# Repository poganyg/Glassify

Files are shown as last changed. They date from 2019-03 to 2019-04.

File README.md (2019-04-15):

<p align="center">
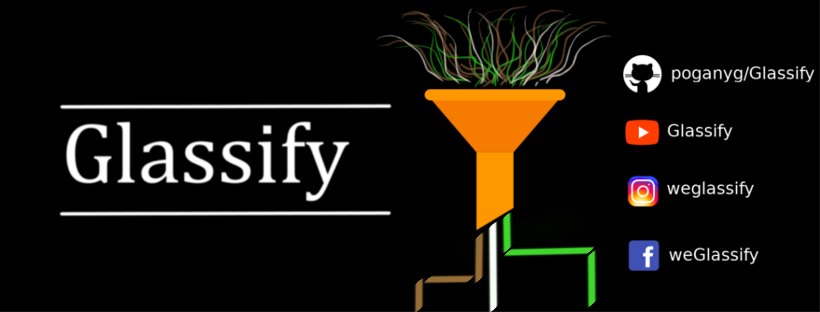
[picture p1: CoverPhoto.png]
Glassify cover photo
   
</p>

# Introduction

We are bringing you a colour-based glass recycling sorter which can separate, in real-time, green, amber and clear bottles!
This is a university project for the subject real-time embedded programming. Watch our short introduction to why and how we are building this project:

<p align="center">
  <a href="https://www.youtube.com/watch?v=iapjhaJnOS8" target="_blank">
  A video summary of Glassify 
  </a>
</p>

## Motive

Glass is 100% recyclable and by doing so we can substantially reduce raw materials needed, the waste produced as well as water and air pollution.<sup>[1](https://www.glassrecycle.co.uk/Why-Recycle/Facts--Figures/)</sup> However, contamination is a major factor in the effectiveness of recycling.<sup>[2](https://wasterecycling.org/news/426888/NWRA-Celebrates-America-Recycles-Day.htm)</sup> This can be due to non-glass materials disposed alongside with the bottles, such as bottle caps, but also by mixing differently coloured glasses. Colours are achieved by adding impurities, such as sulfur, copper or iron to the glasses. Their purpose is to protect the contents from environmental effects. Even one colour misplaced in the wrong bin can deteriorate the quality of the recycled glass. <sup>[3](https://recyclenation.com/2014/09/recycling-glass-does-color-matter/)</sup> This project aims to achieve a more effective glass recycling to preserve our natural resources and protect our environment. 

## Our Solution

We are presenting here a device which can be installed to recycling points to assisst with the user-side recycling process. Once installed, a single input can be used for the glass recycling bin and the internal sorting would ensure that colour contamination doesn't occur. The device uses a Raspberry Pi microcontroller and is built using 3D printing which means that the overall production cost can be kept under £100. 

<p align="center">
  <a href="https://www.youtube.com/watch?v=UAzmWVJm4zI" target="_blank">
  A video summary of Glassify 
  </a>
</p>

# Have we got your fascination?

To see updates follow us on Facebook, YouTube and Instagram.

If you would like to recreate this project, head over to our [Wiki](https://github.com/poganyg/Glassify/wiki) page where you will find a detailed building guide including a list of all the components you will need for building it. In terms of software requirements, you will need to install:

* [openCV](https://opencv.org/releases.html)
* [Raspicam](http://www.uco.es/investiga/grupos/ava/node/40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)
* [WiringPi](http://wiringpi.com/download-and-install/)
* [CMake](https://cmake.org/install/)
* [Git](https://git-scm.com/downloads) (Optional, makes cloning this repository easier.)

Do make sure to only have these installed once on your Raspberry Pi.

To build our software run the following code in your terminal:
```
git clone https://github.com/poganyg/Glassify.git
cd Glassify
mkdir build
cd build
cmake ..
make
```

The project is under the GNU General Public License v3.0.

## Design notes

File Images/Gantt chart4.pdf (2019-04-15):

ea
te Glassify | SIMPLE GANTT CHART by Vertex42.com (https://www.vertex42.com/ExcelTemplates/simple-gantt-chart.html)

Enter Company Name in cell B2. Ross Crawford

https://www.vertex42.com/ExcelTemplates/simple-gantt-chart.html

Enter the name of the Project Lead in cell B3. Enter the Project Start date in cell E3. Pooject Start: label is in cell C3. Reuben Docea | Project Start:

e
Di

### Gergely Pogany

Display Week:

1

lls | 11 12 13 14 15 16 17 | 18 19 20 21 22 23 24 | 25 26 27 28 1 2 3 | 4 5 6 7 8 9 10 | 11 12 13 14 15 16 17 | 18 19 20 21 22 23 24 | 25 26 27 28 29 30 31 | 1 2 3 4 5 6 7 | 8 9 10 11 12 13 14
is
ro
TASK | ASSIGNED
TO
START | END | M | T | W | T | F | S | S | M | T | W | T | F | S | S | M | T | W | T | F | S | S | M | T | W | T | F | S | S | M | T | W | T | F | S | S | M | T | W | T | F | S | S | M | T | W | T | F | S | S | M | T | W | T | F | S | S | M | T | W | T | F | S | S

ll
B8 Design and Setup

ll
B9 | Learning C++ | All | 10/02/19 | 28/02/19

o
w
Hardware Concept | All | 15/02/19 | 18/02/19
Installing Necessary Libraries | Reuben | 20/02/19 | 22/02/19
In-depth Hardware Design | Reuben + Ross | 22/02/19 | 02/03/19

e
ce

Software Development

LCD Scripts | Gergely | 01/03/19 | 10/03/19
Classification Scripts | Reuben | 01/03/19 | 19/03/19
Switch Polling | Ross | 04/03/19 | 11/03/19
Motor Scripts | Gergely | 06/03/19 | 12/03/19
Menu Coding | Gergely | 11/03/19 | 17/03/19
Compiling and Threading | Ross | 11/03/19 | 27/03/19

Sample phase title block Hardware Development

Ordering Suitable Components | Gergely | 02/03/19 | 03/03/19
Modelling Parts | Reuben + Ross | 02/03/19 | 13/03/19
PCB Design | Gergely | 02/03/19 | 13/03/19
Part Priniting | Reuben | 03/03/19 | 15/03/19
Assembly | All | 15/03/19 | 19/03/19

Sample phase title block Optimisation

Testing Software | Reuben | 28/03/19 | 03/04/19
Testing Hardware | Ross | 28/03/19 | 03/04/19
Improvements from Tests | All | 03/04/19 | 14/04/19

15/02/2019

Feb 11, 2019 | Feb 18, 2019 | Feb 25, 2019 | Mar 4, 2019 | Mar 11, 2019 | Mar 18, 2019 | Mar 25, 2019 | Apr 1, 2019 | Apr 8, 2019

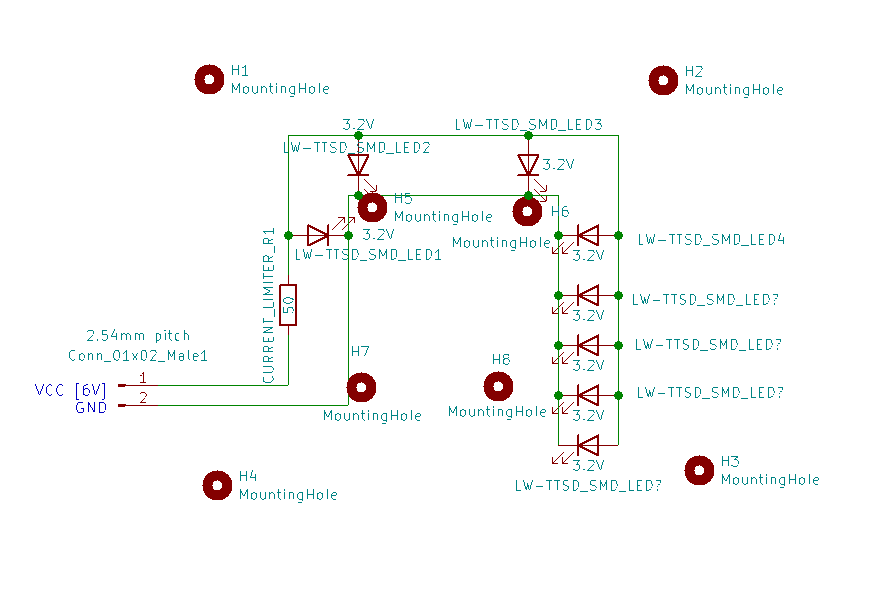
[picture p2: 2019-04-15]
Images/LED_board_schematic_cropped.png

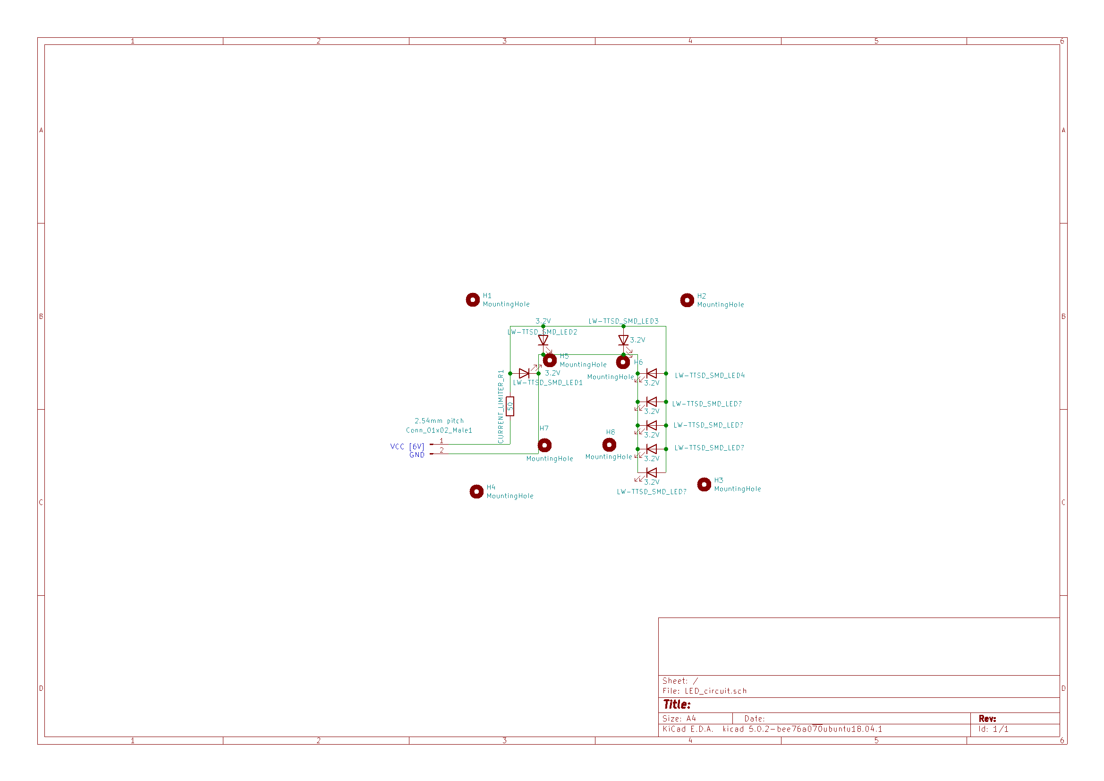
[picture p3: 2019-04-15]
Images/LED_board_schematic.png

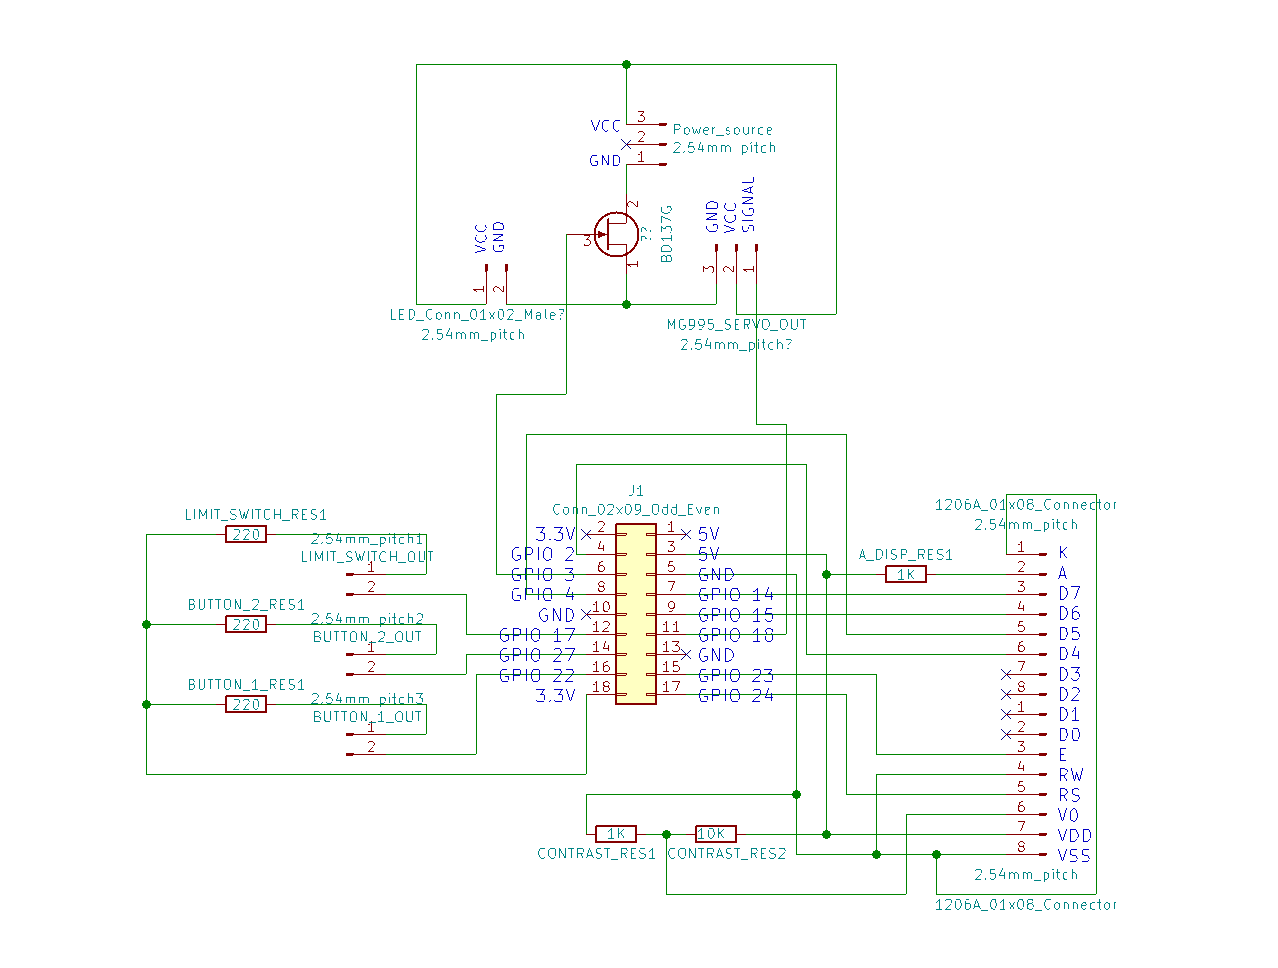
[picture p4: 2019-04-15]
Images/main_board_schematic_cropped.png

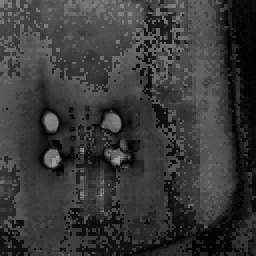
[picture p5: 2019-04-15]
Images/bottle03.jpg

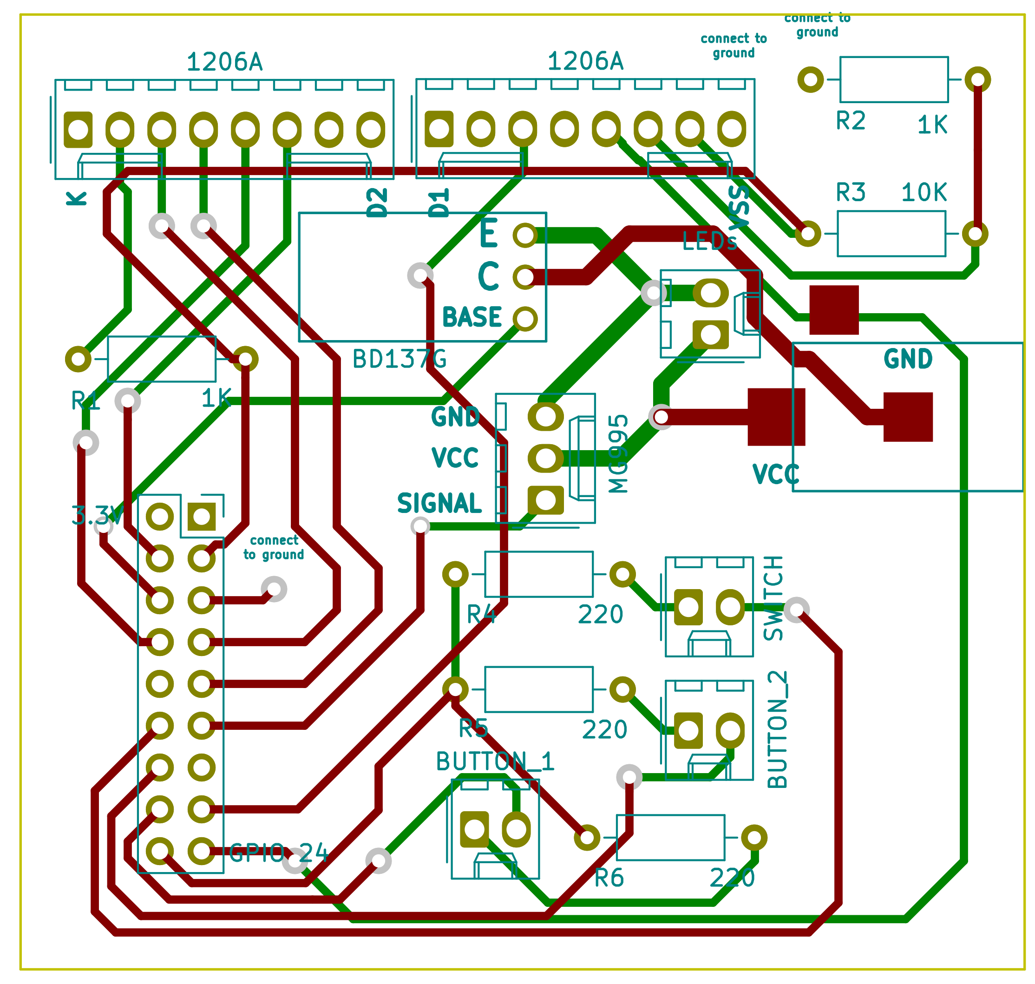
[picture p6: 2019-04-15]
Images/glassify-brd.png

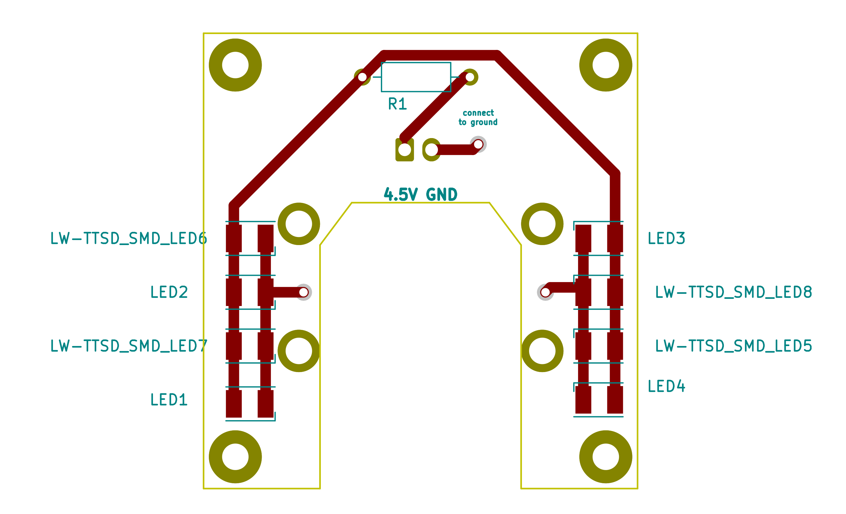
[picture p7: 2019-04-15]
Images/LED_circuit-brd.png

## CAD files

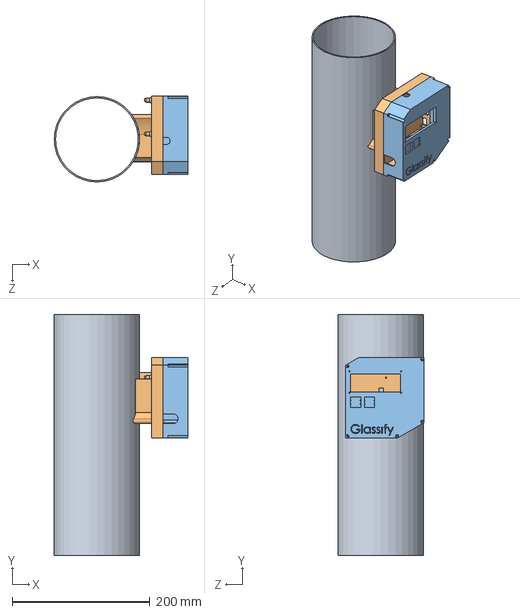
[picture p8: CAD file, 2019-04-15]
hardware/3DModels/Electronics/ElectronicsAssembly.SLDASM
194.0 x 350.0 x 124.8 mm
ElectronicsHousing
ElectronicsHousingCover

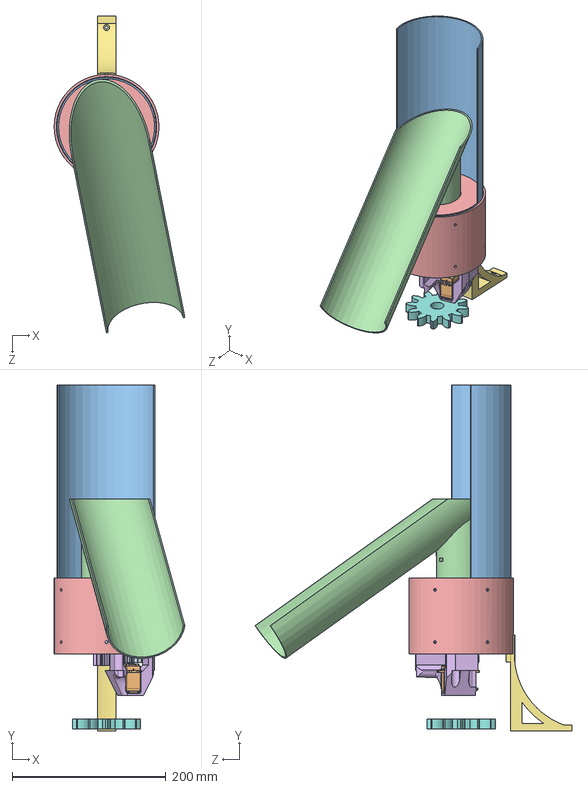
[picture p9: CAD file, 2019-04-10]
hardware/3DModels/Assembly.SLDASM
170.2 x 450.0 x 412.4 mm
WheelBarNarrower x 7
WheelEnlarged x 7
TopRing
ShaftClamp
ServoGear
ROBOT SERVO Hitec HSR-2645CR
BaseDrillGuide
NewServoCarriage
SorterStand

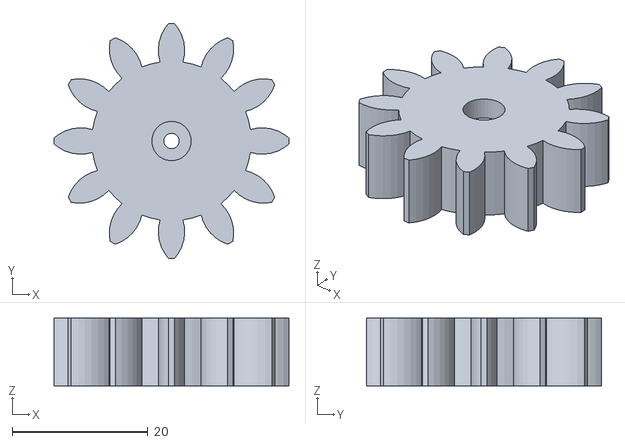
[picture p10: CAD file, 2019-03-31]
hardware/3DModels/STL Files/ServoGear.STL
34.7 x 34.7 x 10.0

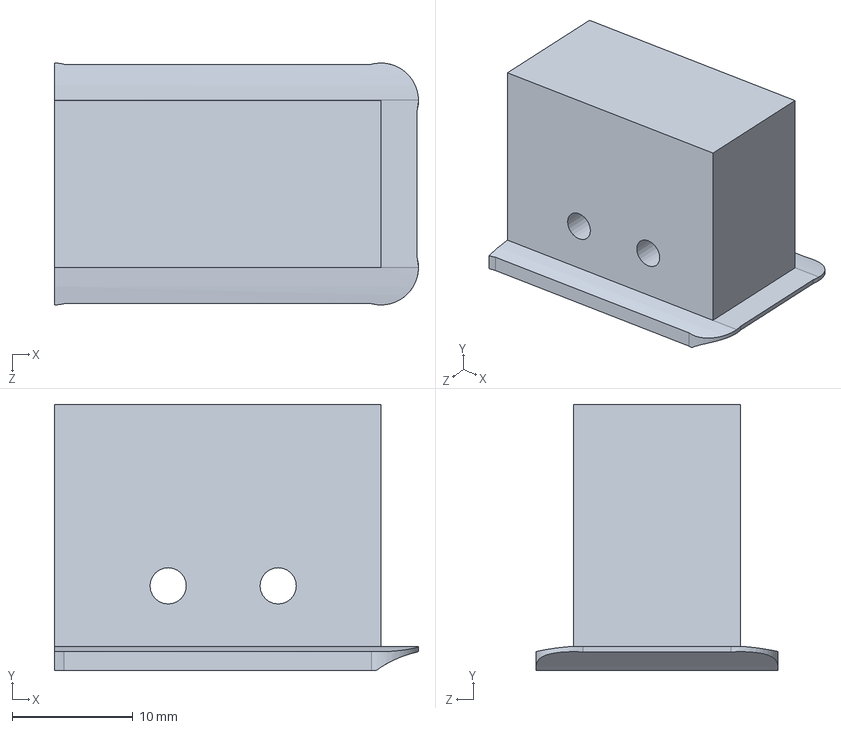
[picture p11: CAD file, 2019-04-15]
hardware/3DModels/switchHolder.SLDPRT
30.1 x 22.0 x 20.0 mm

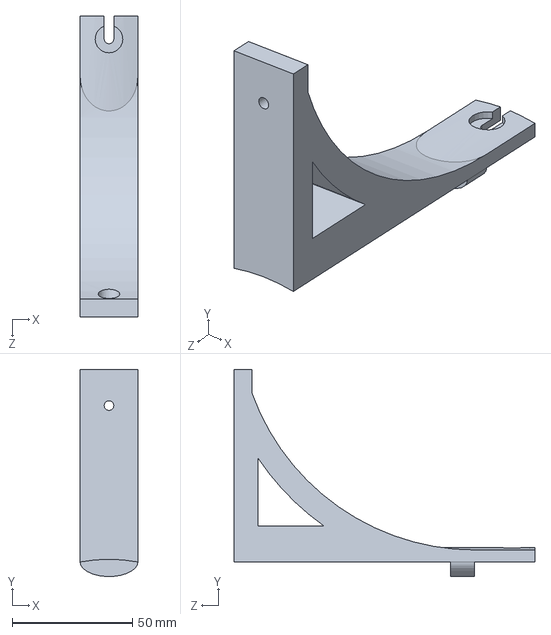
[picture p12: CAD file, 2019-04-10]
hardware/3DModels/SorterStand.sldprt
24.0 x 86.0 x 125.0 mm

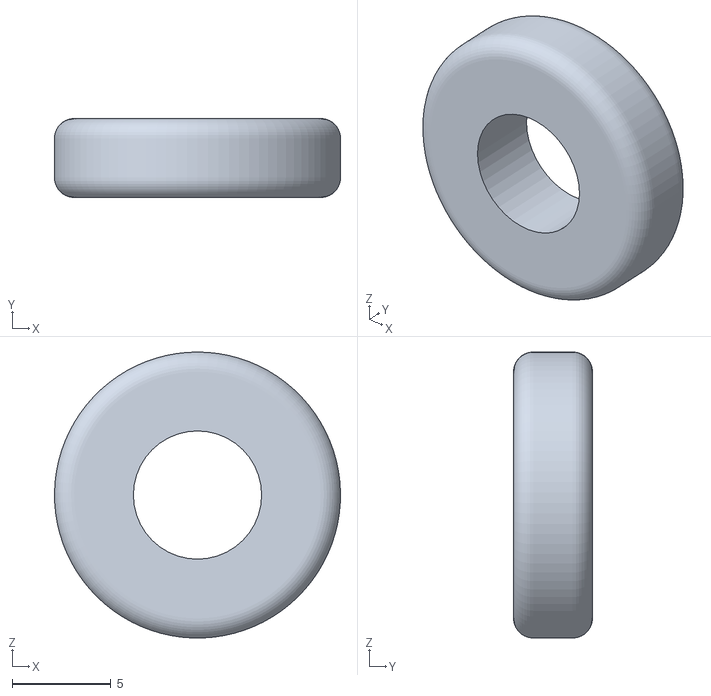
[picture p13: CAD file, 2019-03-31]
hardware/3DModels/STL Files/Wheel.STL
14.5 x 4.00 x 14.5

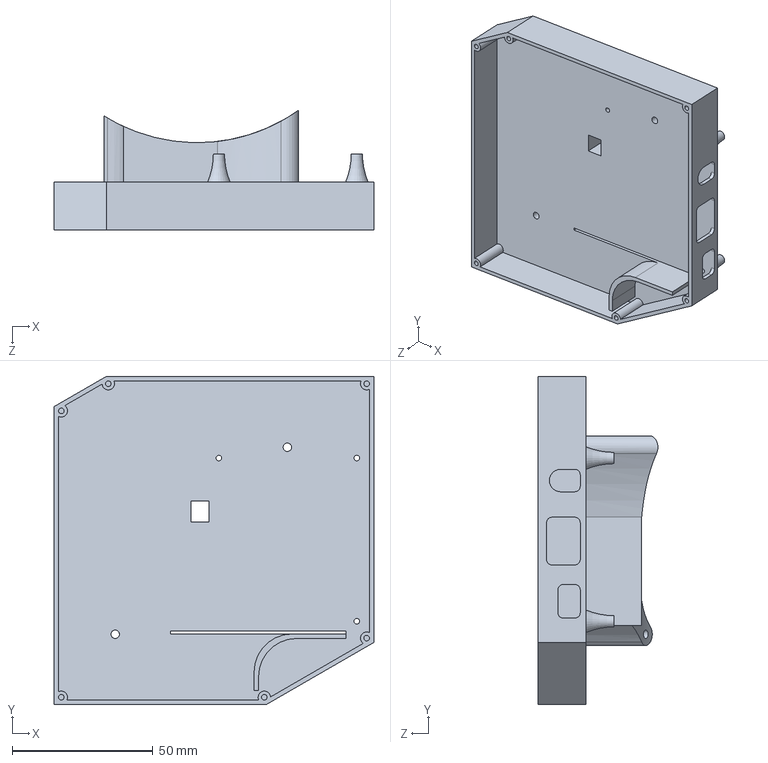
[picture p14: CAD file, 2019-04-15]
hardware/3DModels/Electronics/ElectronicsHousing.sldprt
113.7 x 116.6 x 42.6 mm

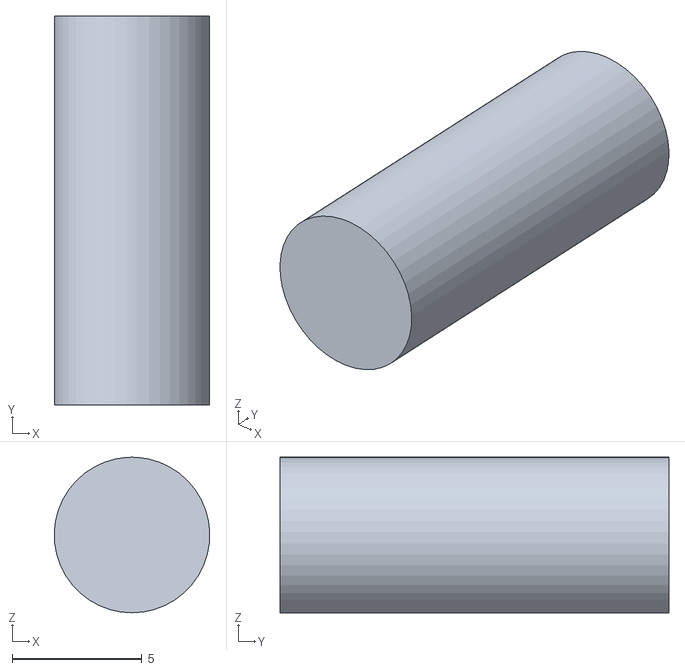
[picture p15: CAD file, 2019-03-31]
hardware/3DModels/STL Files/WheelBar.STL
6.00 x 15.0 x 6.00

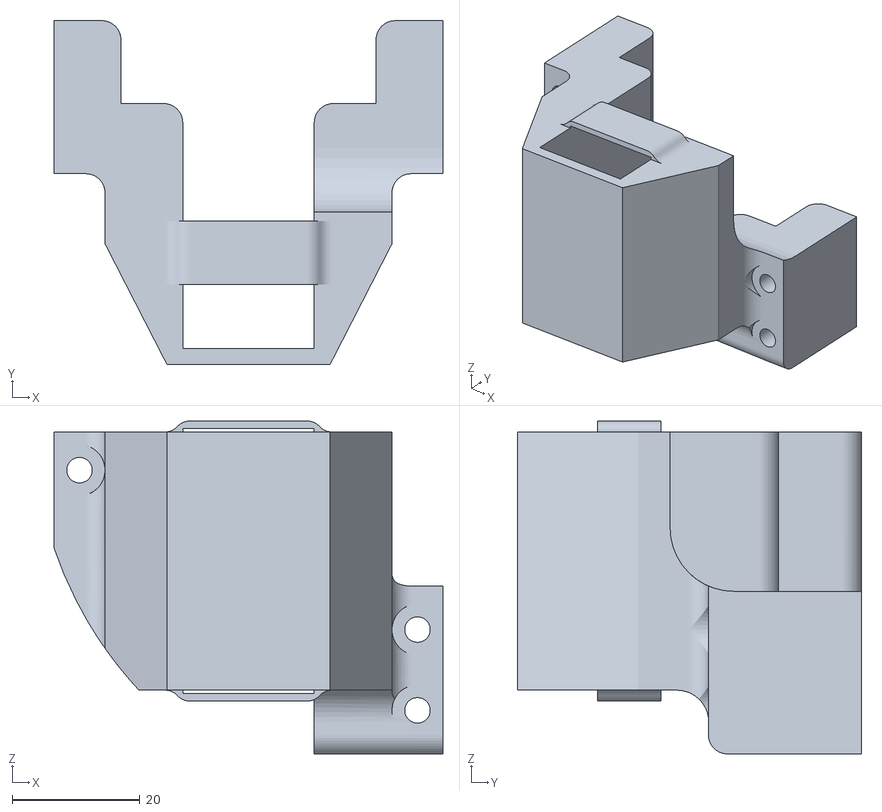
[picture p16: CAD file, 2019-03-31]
hardware/3DModels/STL Files/ServoCarriage.STL
61.0 x 53.9 x 52.2

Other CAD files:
hardware/3DModels/Electronics/ElectronicsHousingCover.sldprt
hardware/3DModels/TestNewServoGear6mm.SLDPRT
hardware/3DModels/TestNewServoGear5_95mm.SLDPRT
hardware/3DModels/BaseDrillGuide.sldprt
hardware/3DModels/TestNewServoGear5_65mm.SLDPRT
hardware/3DModels/TestNewServoGear5_75mm.SLDPRT
hardware/3DModels/NewServoGear.sldprt
hardware/3DModels/FunnelJoinDrillGuide.sldprt
hardware/3DModels/Funnel Drill Guide.sldprt
hardware/3DModels/BoltGuard.sldprt
hardware/3DModels/BoltGuardAssembly.sldasm
hardware/3DModels/BottomRing.SLDPRT
hardware/3DModels/Electronics/ElectronicsHousing.STL
hardware/3DModels/Electronics/ElectronicsHousingCover.STL
hardware/3DModels/Gear.SLDPRT
hardware/3DModels/NewServoCarriage.sldprt
hardware/3DModels/RotatingPortion.SLDPRT
hardware/3DModels/STL Files/BoltGuard.STL
hardware/3DModels/STL Files/BottomRing.STL
hardware/3DModels/STL Files/Funnel Drill Guide.STL
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

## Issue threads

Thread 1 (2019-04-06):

Classification requires configuration for Raspberry Pi camera

Rusk-Cramford, 2019-04-06:
The Classification script currently runs functionally on webcams but requires configuration for the raspberry Pi camera and the lighting conditions withing the tube.

Docea, 2019-04-06:
This has been achieved.

Closed 2019-04-06.

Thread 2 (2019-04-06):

Electronics Housing to be completed

Docea, 2019-04-06:
The Electronics housing is currently incomplete and requires testing

Docea, 2019-04-08:
Design must be adjusted for:
BOTTOM:
- The LED PCB is going to change
- Audio Jack
- HDMI
- Power In
TOP:
- battery pack
- LCD screen
- Buttons for LCD navigation

Docea, 2019-04-09:
made adjustments for LCD, HDMI and Audio jack.

Docea, 2019-04-09:
Perhaps should wait for conclusion on doing away with battery pack?

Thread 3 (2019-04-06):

Testing of Motor and Switch does not test for sustained use

Rusk-Cramford, 2019-04-06:
The script used to test the threads used for polling and motor control does not ensure that they can be used continuously. It only runs once.

Closed 2019-04-06.

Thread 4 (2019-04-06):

Display not working with PCB

Docea, 2019-04-06:
The LCD display works with the raspberry pi on breadboard, but when connecting it to the PCB is does not.

poganyg, 2019-04-07:
The soldering of the GND pins were redone and the LCD now works well with the PCB too.

Closed 2019-04-07.

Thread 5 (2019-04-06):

Must determine top-section of sorter

Docea, 2019-04-06:
It is currently not known what known what the top section of the sorter will consist of, i.e. sloping or what king of lid. This affects the lighting that will be in the tube, and therefore affects the calibration (finalisation) of the classification

Docea, 2019-04-11:
This has been decided. The top is a slanted inlet with a switch to trigger classification.

Closed 2019-04-11.

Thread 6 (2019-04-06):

Classification must be performed in tandem with motor-moving

Docea, 2019-04-06:
The motor must react to the changing of state from the classification from rest to the presence of a bottle.

Docea, 2019-04-08:
This has been achieved by passing pointers to a 'state' class to both the classification object and the motor thread object and monitoring this state through a 'mutex' variable

Docea, 2019-04-08:
This has been achieved by passing pointers to a 'state' class to both the classification object and the motor thread object and monitoring this state through a 'mutex' variable

Closed 2019-04-08.

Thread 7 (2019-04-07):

Classifier object and Motor object read&write to same pointer

Docea, 2019-04-07:
Classifier object and Motor object read&write to same pointer causing segmentation fault.

This may be solved by creating a second pointer variable which indicates to either thread that it is ok to access the variable

Docea, 2019-04-07:
Solved -- threads access same memory via class-based pointer and 'mutex'

Docea, 2019-04-07:
Solved -- threads access same memory via class-based pointer and 'mutex'

Closed 2019-04-07.

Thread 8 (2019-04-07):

The 3D printed servo gear connection to servo loose

Docea, 2019-04-07:
The 3D printer servo gear connection to servo is loose and gets ground away, making it even more loose and unusable. To fix this, middle hole on servo must be made smaller, and bolt from the top may be included for a more snug and secure fit.

poganyg, 2019-04-15:
Resolved by reprinting the gear with a smaller diameter for a tighter fit.

Closed 2019-04-15.

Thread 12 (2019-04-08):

Motor doesn't turn to output for long enough during classification

Docea, 2019-04-08:
The motor flicks between outputs or gets confused under ambiguous signals

Docea, 2019-04-08:
Can be fixed by stabilising the classification output (e.g. 3 identical consecutive decisions give a stable output for 0.5 seconds)

Docea, 2019-04-10:
Completed. Works well.

Closed 2019-04-10.

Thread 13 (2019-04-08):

LED PCB doesn't fit the camera bolt-holes

Docea, 2019-04-08:
The holes for mounting on the camera don't align with those on the LED PCB

poganyg, 2019-04-13:
LED PCB has been redesigned to fit the camera.

Closed 2019-04-13.

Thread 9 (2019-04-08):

Bottles hit tops of bolts securing outlet pipe

Docea, 2019-04-08:
Bottles hit tops of bolts and loud and slows it down. Need to design a 3D printed piece to go inside outlet pipe to smoothly guide bottle.

poganyg, 2019-04-15:
The piece has been printed and the bottles are exiting the device smoother now.

Closed 2019-04-15.

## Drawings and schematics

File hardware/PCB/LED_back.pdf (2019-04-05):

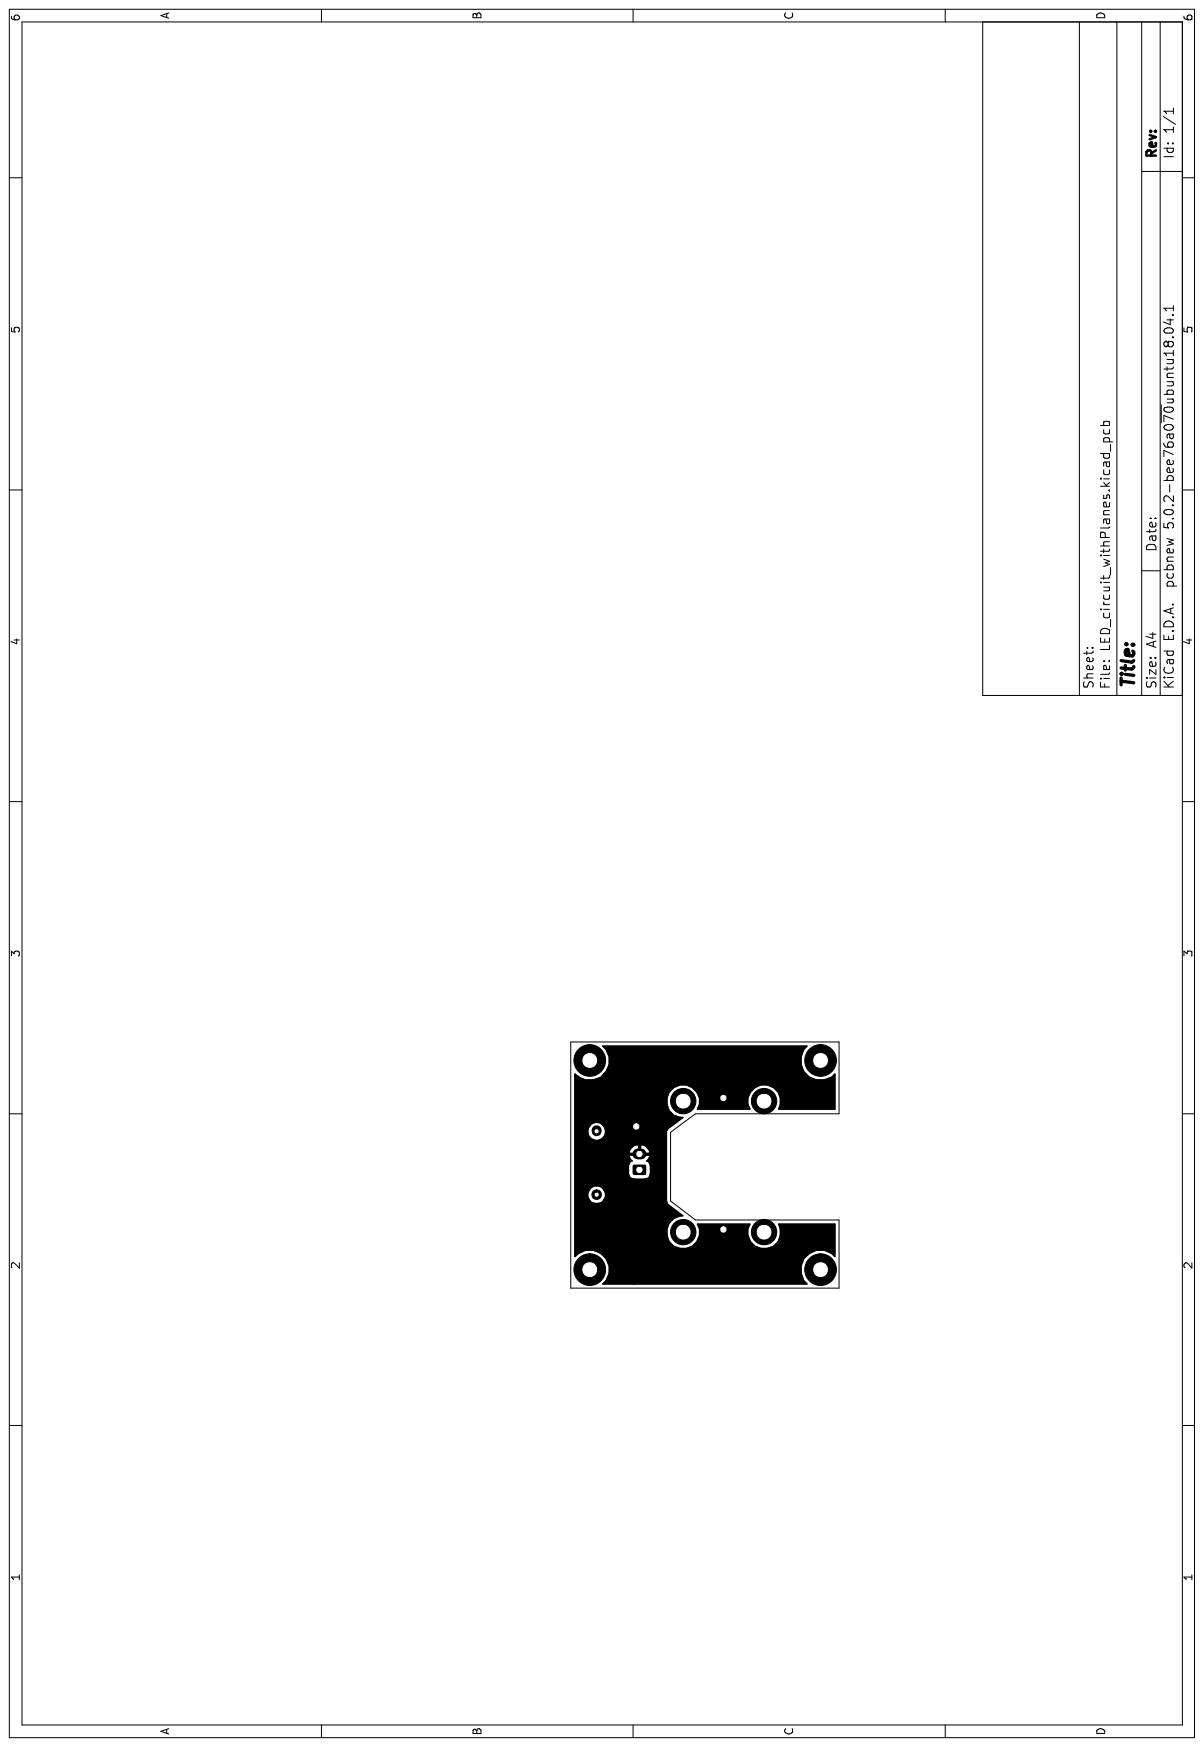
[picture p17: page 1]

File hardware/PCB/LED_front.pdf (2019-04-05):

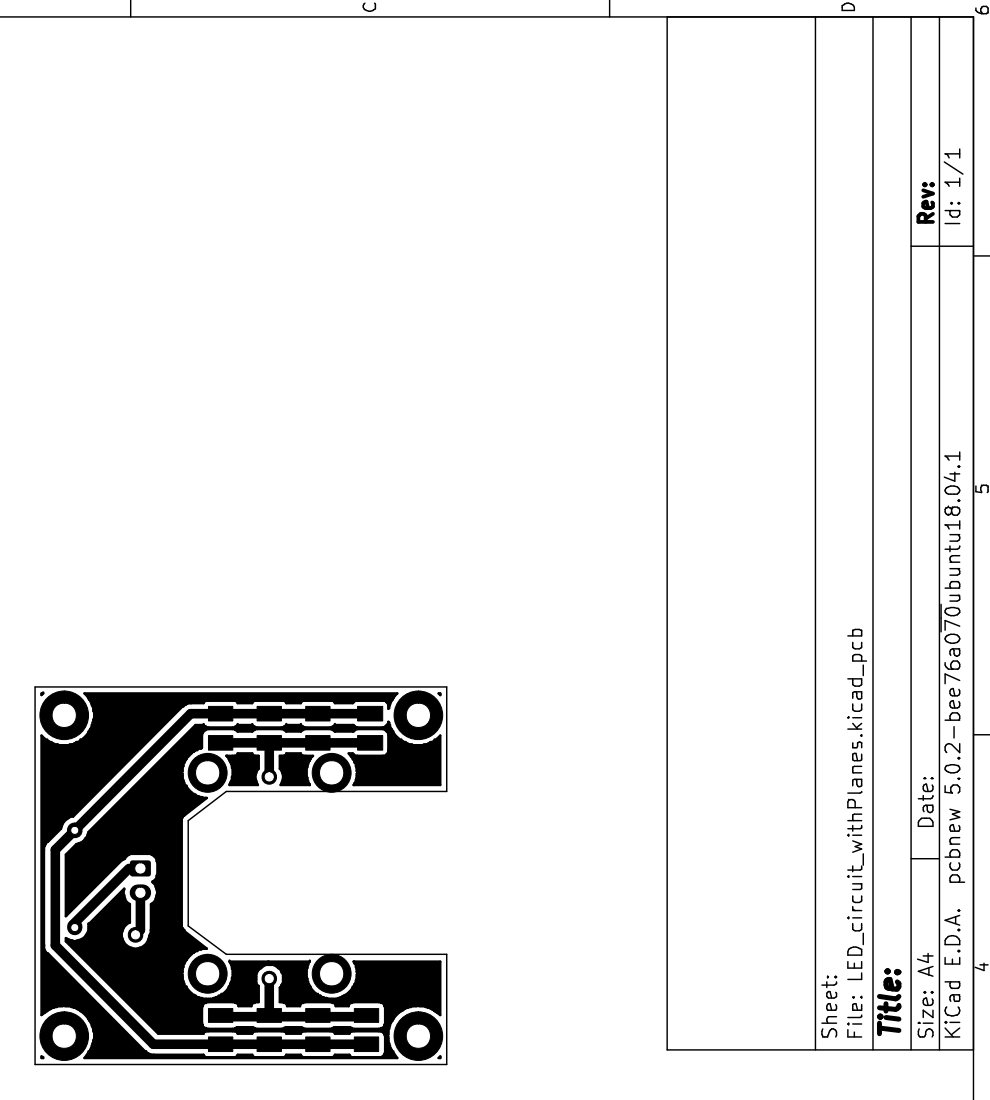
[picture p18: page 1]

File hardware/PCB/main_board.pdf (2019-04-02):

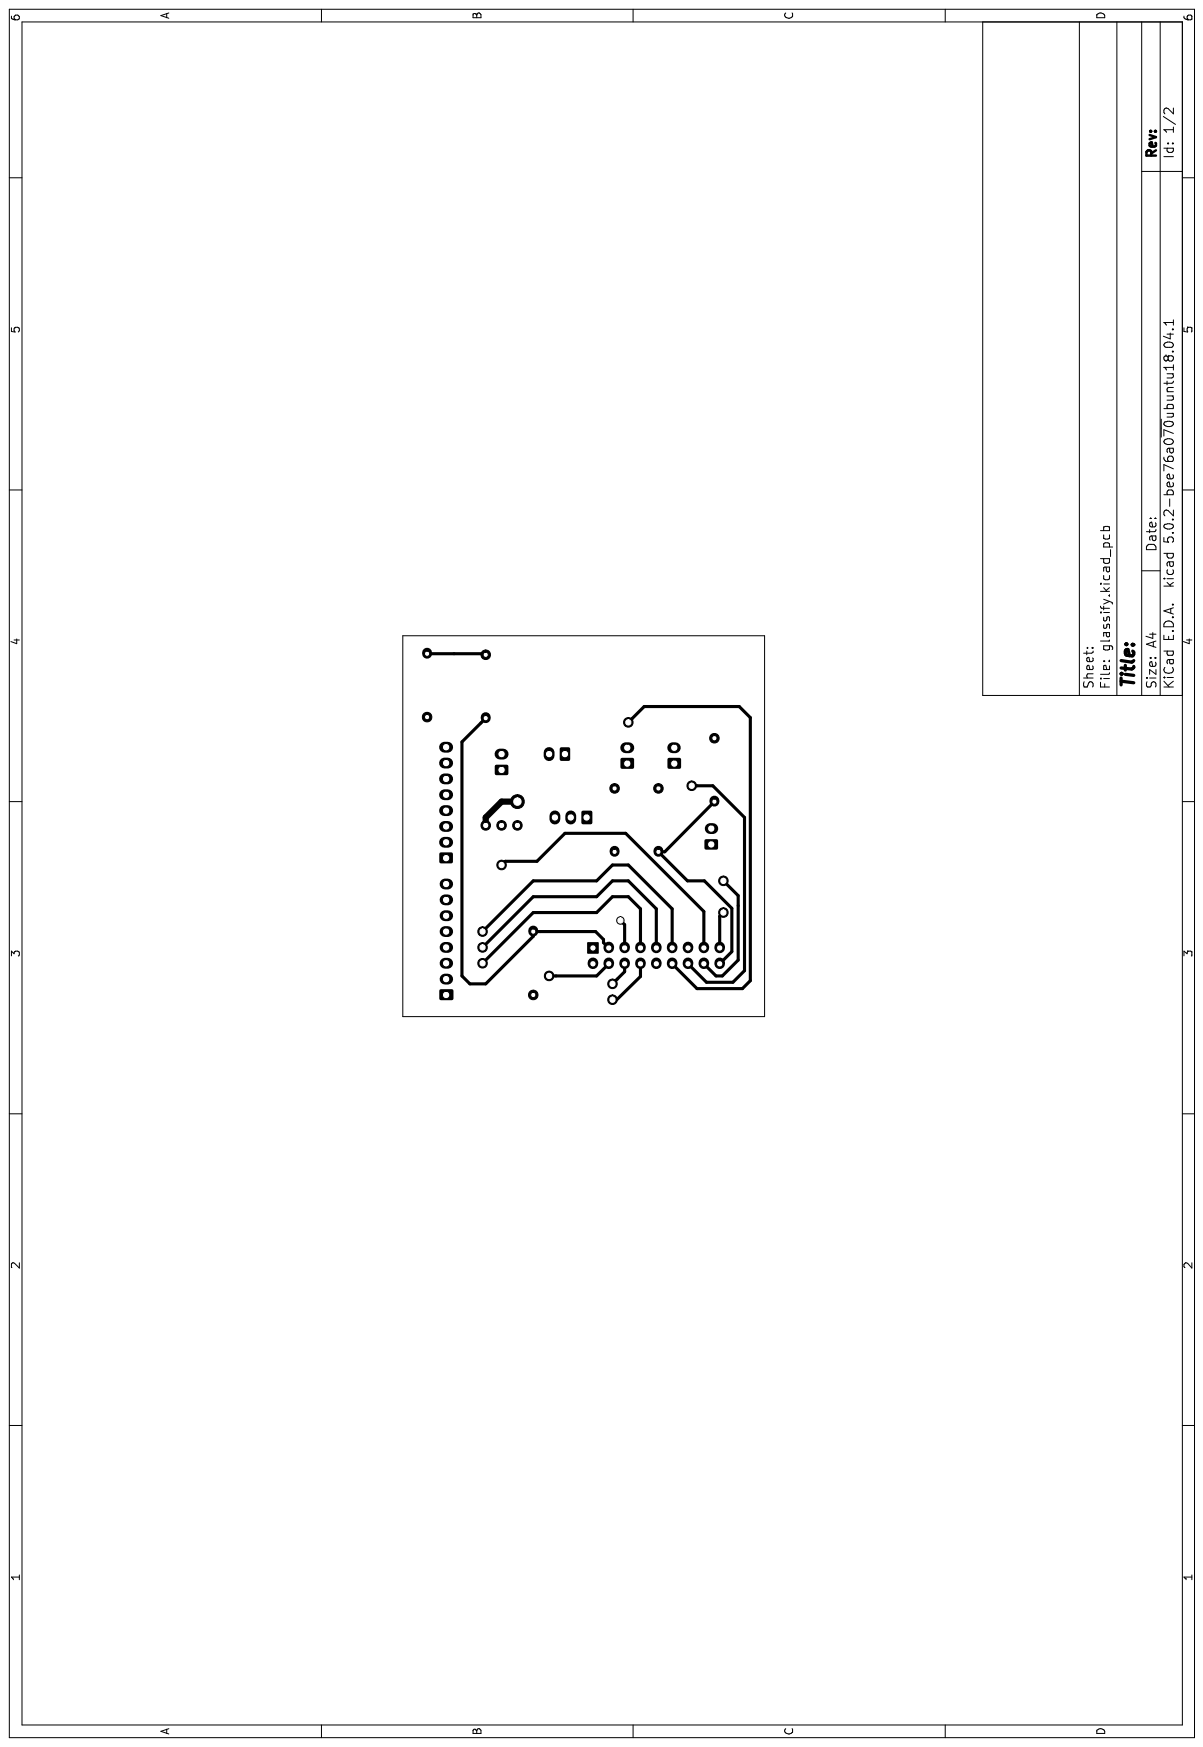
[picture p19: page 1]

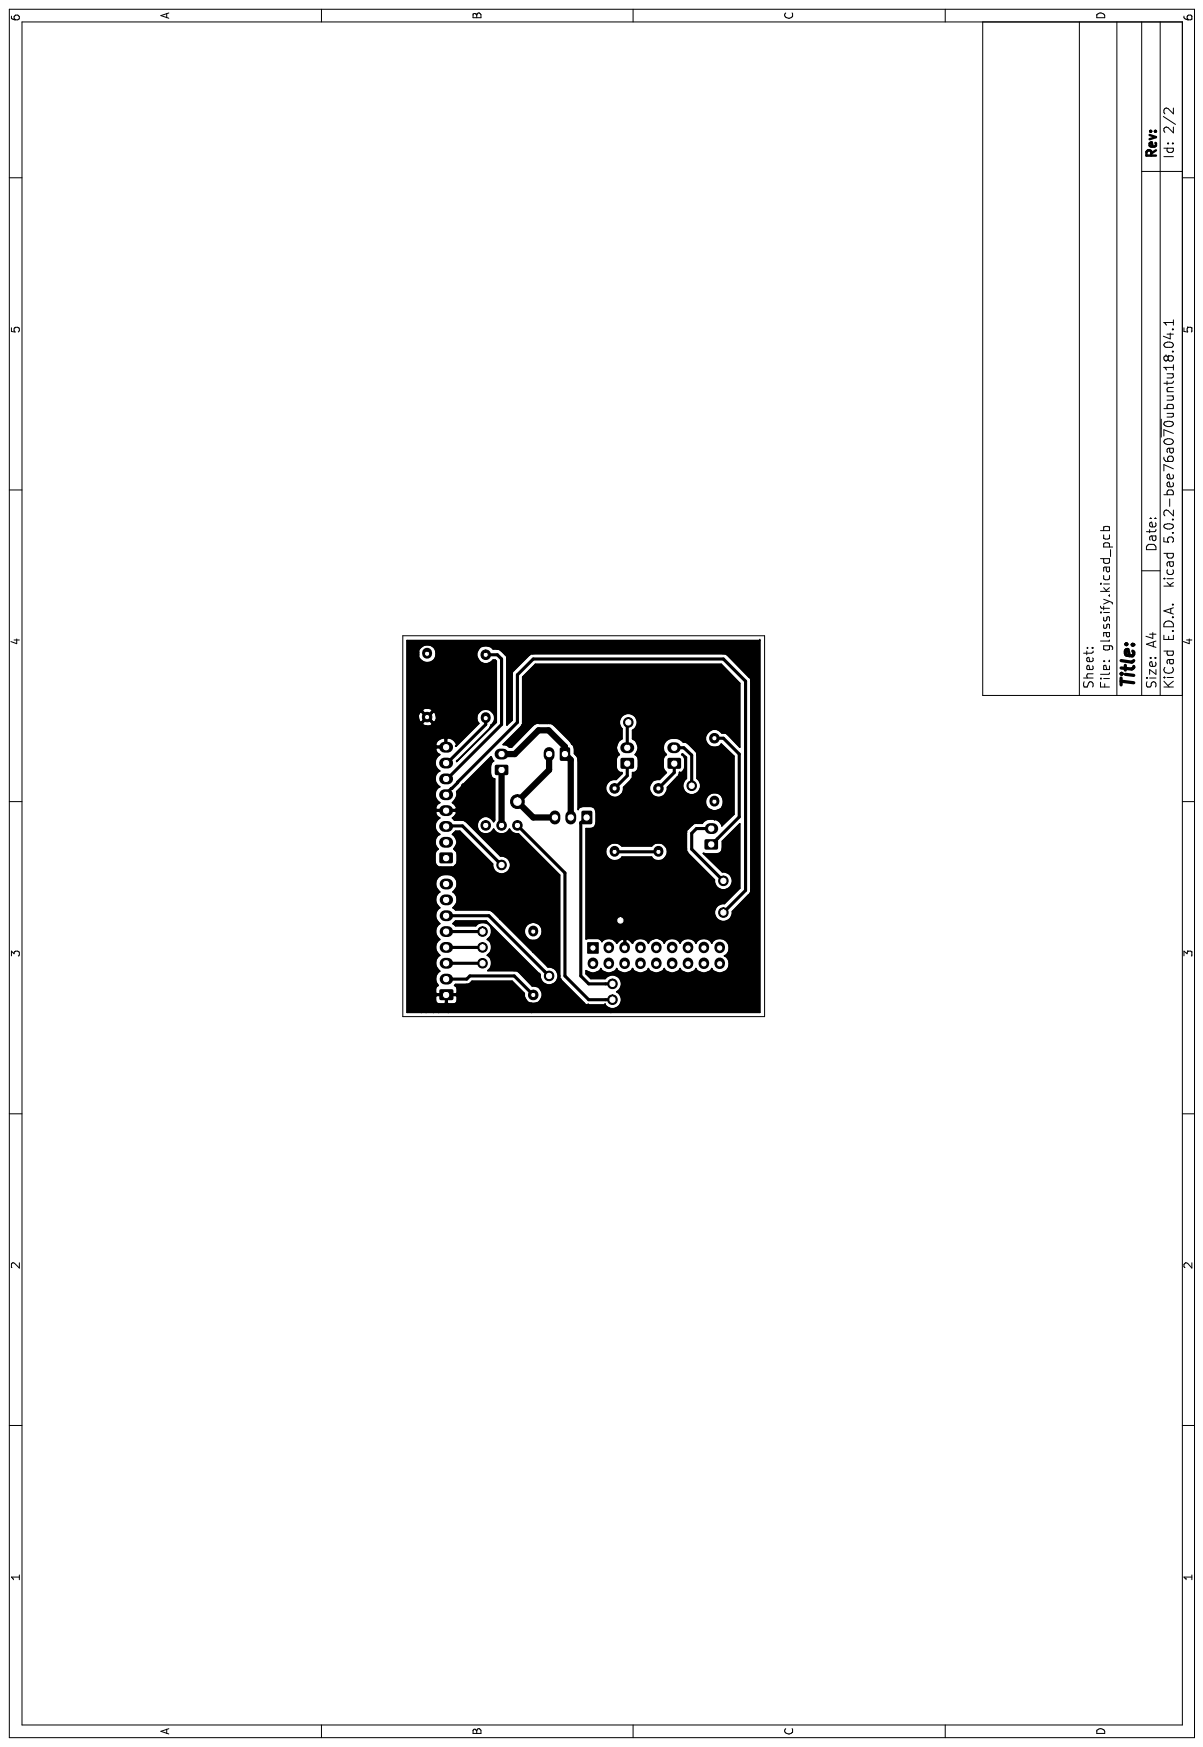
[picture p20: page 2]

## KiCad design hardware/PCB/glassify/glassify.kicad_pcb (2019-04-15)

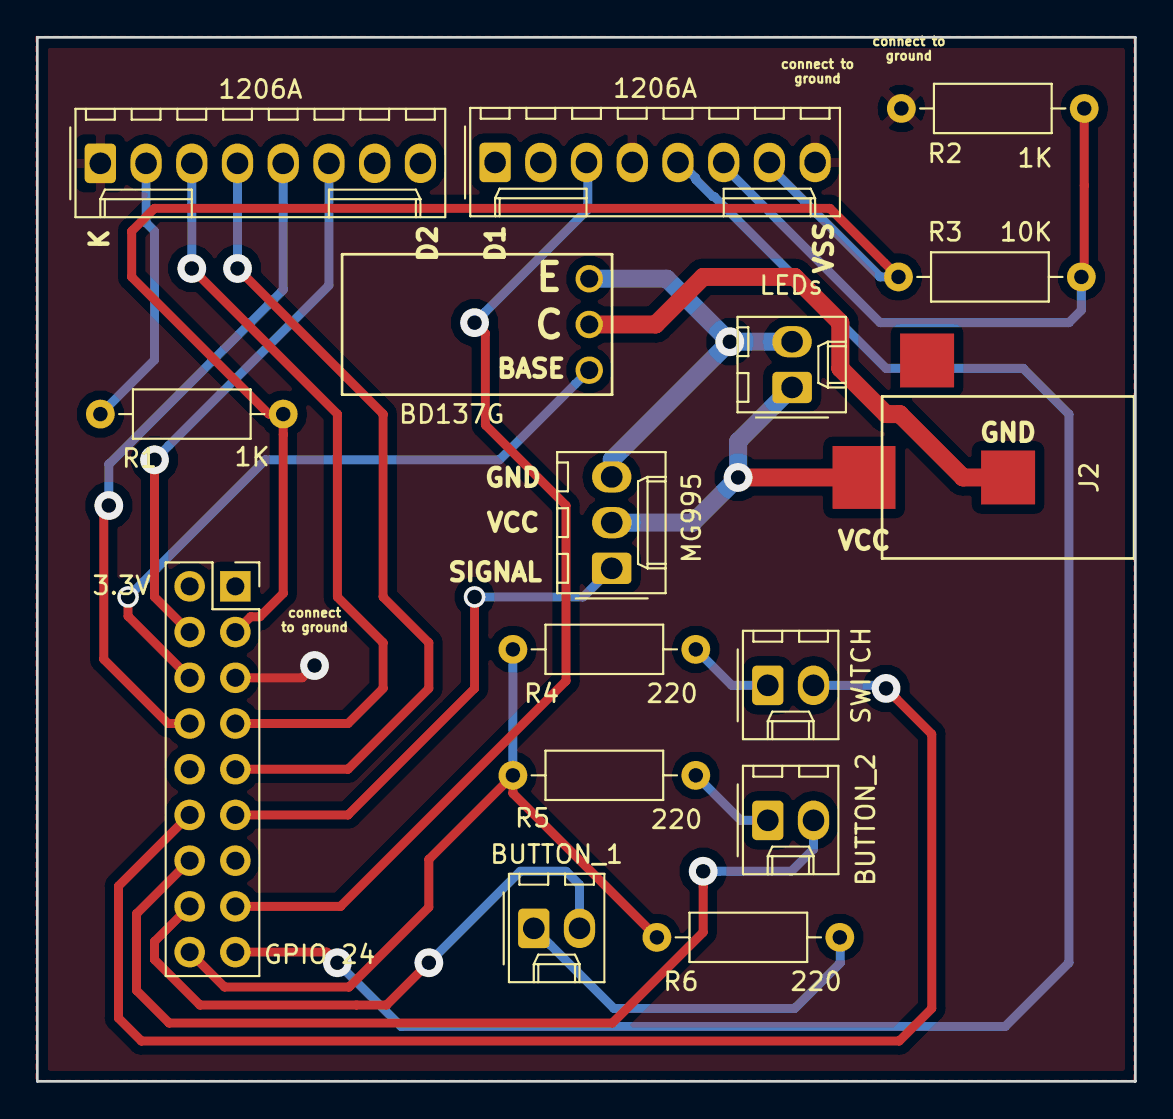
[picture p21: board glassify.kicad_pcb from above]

Board: 2 copper layers, 61.0 x 58.0 mm, 16 parts (0 on the bottom side), 22 nets.

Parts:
1206A, 1206A#2: 2mm_pitch; Molex_KK-254_AE-6410-08A_1x08_P2.54mm_Vertical
BD137G: ??; BD137G
BUTTON_1: BUTTON_1_OUT; Molex_KK-254_AE-6410-02A_1x02_P2.54mm_Vertical
BUTTON_2: BUTTON_2_OUT; Molex_KK-254_AE-6410-02A_1x02_P2.54mm_Vertical
J1: Conn_02x09_Odd_Even; PinSocket_2x09_P2.54mm_Vertical
J2: Conn_01x03_Male; power_adapter_conn
LEDs: 2mm_pitch; Molex_KK-254_AE-6410-02A_1x02_P2.54mm_Vertical
MG995: MG995_SERVO_OUT; Molex_KK-254_AE-6410-03A_1x03_P2.54mm_Vertical
R1, R2: 1K; R_Axial_DIN0207_L6.3mm_D2.5mm_P10.16mm_Horizontal
R3: 10K; R_Axial_DIN0207_L6.3mm_D2.5mm_P10.16mm_Horizontal
R4, R5, R6: 220; R_Axial_DIN0207_L6.3mm_D2.5mm_P10.16mm_Horizontal
SWITCH: LIMIT_SWITCH_OUT; Molex_KK-254_AE-6410-02A_1x02_P2.54mm_Vertical

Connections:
unnamed: R4.1, SWITCH.1
unnamed: J1.12, SWITCH.2
unnamed: BUTTON_2.1, R5.1
unnamed: BUTTON_2.2, J1.14
unnamed: BUTTON_1.1, R6.1
unnamed: BUTTON_1.2, J1.16
unnamed: J1.11, MG995.1
unnamed: J2.3, LEDs.1, MG995.2
unnamed: BD137G.1, LEDs.2, MG995.3
unnamed: 1206A.1, 1206A#2.4, 1206A#2.8, J1.5, R2.1
unnamed: 1206A.2, R1.1
unnamed: 1206A.3, J1.7
unnamed: 1206A.4, J1.9
unnamed: 1206A.5, J1.8
unnamed: 1206A.6, J1.4
unnamed: 1206A#2.3, J1.15
unnamed: 1206A#2.5, J1.17
unnamed: 1206A#2.6, R2.2, R3.1
unnamed: 1206A#2.7, J1.3, R1.2, R3.2
unnamed: BD137G.2, J2.1
unnamed: BD137G.3, J1.6
unnamed: J1.18, R4.2, R5.2, R6.2

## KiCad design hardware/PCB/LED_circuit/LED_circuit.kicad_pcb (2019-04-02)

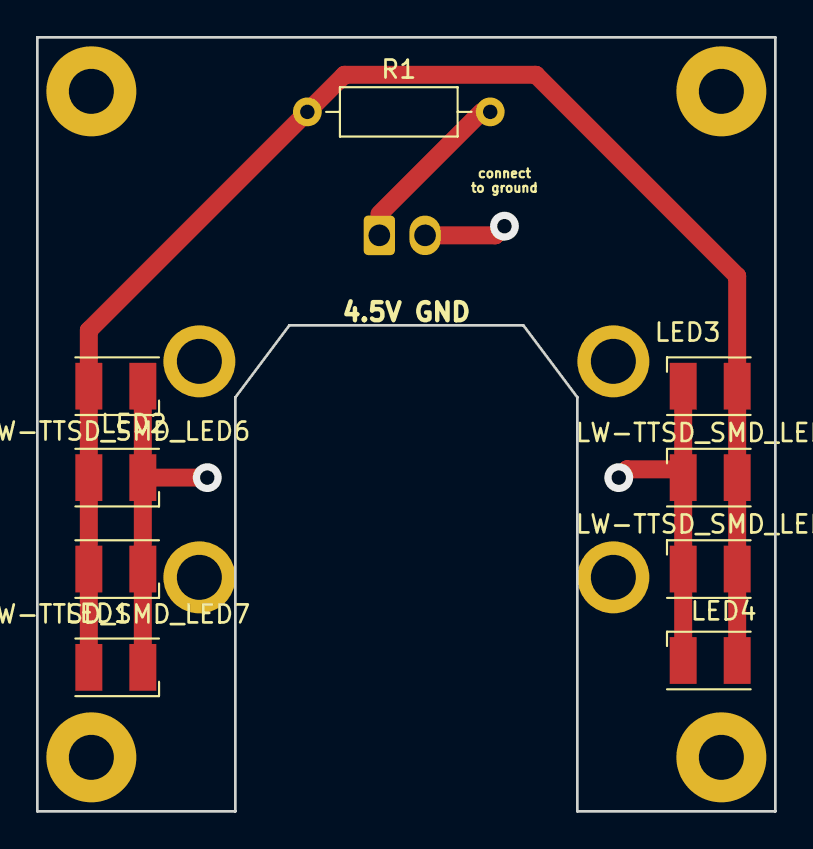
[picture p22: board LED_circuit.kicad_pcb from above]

Board: 2 copper layers, 41.0 x 43.0 mm, 17 parts (0 on the bottom side), 2 nets.

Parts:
H1, H2, H3, H4, H5, H6, H7, H8: MountingHole; MountingHole_2.5mm_Pad
LED1, LED2, LED3, LED4: 3.2V; LED_PLCC-2
LW-TTSD_SMD_LED5, LW-TTSD_SMD_LED6, LW-TTSD_SMD_LED7, LW-TTSD_SMD_LED8: 3.2V; LED_PLCC-2
R1: 16; R_Axial_DIN0207_L6.3mm_D2.5mm_P10.16mm_Horizontal

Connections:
unnamed: LED1.2, LED2.2, LED3.2, LED4.2, LW-TTSD_SMD_LED5.2, LW-TTSD_SMD_LED6.2, LW-TTSD_SMD_LED7.2, LW-TTSD_SMD_LED8.2, R1.1
unnamed: LED1.1, LED2.1, LED3.1, LED4.1, LW-TTSD_SMD_LED5.1, LW-TTSD_SMD_LED6.1, LW-TTSD_SMD_LED7.1, LW-TTSD_SMD_LED8.1

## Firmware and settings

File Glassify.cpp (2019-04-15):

/** @file Glassify.cpp
* @brief Main file which uses all previously written functions
* @author Reuben Docea
*/

#include <wiringPi.h>
#include <iostream>
#include <stdio.h>
#include "./include/state.h"
#include "./include/libServo.h"
#include "./include/Camera.h"
#include "./include/Display.h"
#include "./include/Menu.h"
#include "./include/SwitchThread.h"
#include "./include/MotorThread.h"
#include "./include/Classifier.h"
#include "./include/ClassifierThread.h"
#include "./include/MenuThread.h"
#include "./include/ActivePollThread.h"
#include "Buttons.h"
/**
* @brief Activates all threads in sequence to classify glass and run menu
*/
int main()
{
  //INITIALISATION
  wiringPiSetup();
  State state;		  	 // Initialises state class
  State* stateptr= &state;	 //Sets up pointer to state class
  Servo servo(1); 	  	 //Initialises servo at pin 1
  Servo* servoptr = &servo; 	 //sets up pointer to servo class
  Camera camera; 		 // Initialises Camera class
  Camera* cameraptr = &camera;   //sets up pointer to servo class
  Buttons button(stateptr); // Creates instance of the Buttons class
  Buttons* buttonptr = &button; // Initialises pointer to the button class`
  Display display; 		 //Initialises display class
  Display* displayptr = &display;// Sets up pointer to display class
  Menu menu(displayptr,servoptr,stateptr,buttonptr);// Initialises menu class
  Menu* menuptr = &menu; 	 //sets pointer to menu class
  Classifier classifier(stateptr,cameraptr,servoptr);// Initialises classifier
  Classifier* classifierptr = &classifier; 	//Sets pointer to classifier
  ClassifierThread classifierThread(classifierptr); //Initialises classifier thread
  MotorThread motorThread(stateptr,servoptr);	 //Initialises motor thread
  MenuThread menuThread(menuptr); 		//Initialises menu thread

  ActivePollThread activePollThread(stateptr,17); //initialises active polling thread

  //MAIN SCRIPT
  while(true){
    menuThread.start();
    while(true){
      cout << "REENTERED" << endl;
      SwitchThread switchThread(stateptr,17); 	//Initialises switch thread
      switchThread.start();
      switchThread.join();
      classifierThread.start();
      switchThread.~SwitchThread();
      while(stateptr->getBuffer()!=0)
      {
      ActivePollThread activePollThread(stateptr,17); //initialises active polling
      activePollThread.start();
      activePollThread.join();
      activePollThread.~ActivePollThread();
      };
      classifierThread.join();
    }
    menuThread.join();
  }
}

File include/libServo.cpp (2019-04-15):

#include "libServo.h"
using namespace std;

Servo::Servo(int pin)
:m_pin(pin),pwmClock(384),pwmRange(1000)
{
  pinMode(m_pin, PWM_OUTPUT);
  pwmSetMode(PWM_MODE_MS);
  pwmSetClock(pwmClock);
  pwmSetRange(pwmRange);

  string line;
  ifstream calibFile ("../include/calibration_values");

  getline (calibFile,line);
  m_clearAngle = std::stoi( line );
  getline (calibFile,line);
  m_HaltTime = std::stoi( line );
  getline (calibFile,line);
  m_SepAngle = std::stoi( line );

  calibFile.close();
  m_brownAngle=m_clearAngle - m_SepAngle;
  m_greenAngle=m_clearAngle + m_SepAngle;

  cout << m_clearAngle << endl;
  cout << m_HaltTime << endl;
  cout << m_SepAngle << endl;

  Servo::init();
}

void Servo::init()
{
  float t=m_clearAngle*100/180+25;
  pwmWrite(this->m_pin, t);
  m_lastDegree=m_clearAngle;
}

void Servo::move(float degree)
{
  float t=degree*100/180+25;
  float t2=abs(m_lastDegree-degree)*100/180;
  pwmWrite(this->m_pin, t);
  m_lastDegree=degree;

  std::this_thread::sleep_for(std::chrono::milliseconds(m_HaltTime));
}

void Servo::moveCalib(float degree)
{
  float t=degree*100/180+25;
  pwmWrite(this->m_pin, t);
  m_lastDegree=degree;
}

void Servo::moveBrown()
{
  Servo::move(m_brownAngle);
}

void Servo::moveClear()
{
  Servo::move(m_clearAngle);
}

void Servo::moveClearCalib()
{
  Servo::moveCalib(m_clearAngle);
}

void Servo::moveGreen()
{
  Servo::move(m_greenAngle);
}

void Servo::setRestPosition(float clearAngle)
{
  this->m_clearAngle=clearAngle;
  Servo::moveClearCalib();
}

int Servo::getRestPosition()
{
  return this->m_clearAngle;
}

void Servo::setHaltTime(int Htime)
{
  this->m_HaltTime=Htime;
}

int Servo::getHaltTime()
{
  return this->m_HaltTime;
}

void Servo::setSepAngle(float SepAngle)
{
  this->m_SepAngle=SepAngle;
  m_brownAngle=m_clearAngle - m_SepAngle;
  m_greenAngle=m_clearAngle + m_SepAngle;
}

int Servo::getSepAngle()
{
  return this->m_SepAngle;
}

void Servo::saveCalibValues()
{
  ofstream calibFile;
  calibFile.open ("../include/calibration_values");
  calibFile << this->m_clearAngle <<endl;
  calibFile << this->m_HaltTime<<endl;
  calibFile << this->m_SepAngle;
  calibFile.close();
}

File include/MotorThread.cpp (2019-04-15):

#include <wiringPi.h>
#include <thread>
//#include <cstdlib>
#include <iostream>
#include "MotorThread.h"
//#include "libServo.h"
//#include "libServo.cpp"


void MotorThread::run()
{
	while(true){

	m_state=stateptr->getState();
	std::cout << "MOTOR GOT STATE >> " << m_state << std::endl;

	if(m_state==1)
	{
		servoptr->moveGreen();
		//std::this_thread::sleep_for(std::chrono::milliseconds(m_delay));
  }
  if (m_state==2)
  {
		servoptr->moveBrown();
		//std::this_thread::sleep_for(std::chrono::milliseconds(m_delay));
  }
  if (m_state==3)
  {
		servoptr->moveClear();
		//std::this_thread::sleep_for(std::chrono::milliseconds(m_delay));
  }
	m_state==0;
	{
		servoptr->moveClear();
  }
}
}

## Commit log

2019-02-22 Add files via upload
    Uploading initial servomotor code
2019-02-22 Add files via upload
    An Alternative servo script
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2019-03-08 adding a simple script to test the camera class
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2019-03-16 Testing the display of button messages on the LCD screen
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2019-03-29 Implemented CMake for compiling of scripts for operation of motors, see: IndependentMotors
2019-03-29 Removing folders no longer needed for operation of motors as all required is contained within 'IndependentMotors'
    [libServo.cpp]
2019-03-29 Adding provisional hardware models
    [Assembly.SLDASM, Larger Gear.SLDPRT, Rotating Funnel.SLDPRT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]
2019-03-29 Adding the preliminary PCB designs
    [LED_circuit.kicad_pcb, LED_circuit.sch, glassify.kicad_pcb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]
2019-03-29 Moved contents of 'IndependentMotors' into 'Motors' as no longer need sub-directory
    [libServo.cpp]
2019-03-29 Added Processing.h to enable control over camera settings and HSV image processing.
2019-03-30 Added working classification method
    Working classification scheme implemented, simplifying previous version and ready for implementation on raspberry pi
2019-03-31 Uploading second generation of hardware models
    [Assembly.SLDASM, BottomRing.SLDPRT, Larger Gear.SLDPRT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]
2019-03-31 Adding remaining hardware models
    Added remaining hardware models, as well as externally sourced reference designs for gear and servo motor.
    [Assembly.SLDASM, Gear.SLDPRT, ServoCarriage.sldprt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]
2019-03-31 Adding some hardware STLs
    [BottomRing.STL, ServoCarriage.STL, ServoGear.STL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]
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2019-04-01 Moving traces further from edges, moving some traces from top layer to bottom one.
    [glassify.kicad_pcb]
2019-04-02 Adding better-toleranced CAD models. Redesigned ServoCarriage.
    [NewServoCarriage.sldprt, NewServoGear.sldprt, RotatingPortion.SLDPRT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]
2019-04-02 Added LEDs to have the option of installing more if needed, fixed ground layer on main board to be connected everywhere, rewired pins to ease soldering
    [LED_circuit.kicad_pcb, LED_circuit.sch, glassify.kicad_pcb]
2019-04-02 Added two more drill guides and updated STLs
    Drill Guide added for the join between 100mm halfpipe and rotating portion
    Drill guide for join between two 120mm pipes added
    Added remaining .STL files for new parts and remaining SLDPRT files
    [BottomRing.STL, Funnel Drill Guide.STL, Funnel Drill Guide.sldprt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]
2019-04-04 Added Provisional.h, more efficient & object-oriented
    Script contains a more efficient and object-oriented approach to creating the camera class and performing classification
2019-04-04 Adding a ground plane to the front of the board too.
    [LED_circuit_withPlanes.kicad_pcb, glassify_withPlanes.kicad_pcb]
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2019-04-04 Fixing the distance between drilling holes on the LED board
2019-04-04 fixing backside gnd layer
    [LED_circuit_withPlanes.kicad_pcb]
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2019-04-05 Resolved issues with Motor class communication
    [MotorThread.cpp]
2019-04-05 First half of electronics housing
    [ElectronicsAssembly.SLDASM, ElectronicsHousing.STL, ElectronicsHousing.sldprt]
2019-04-05 Resolved issues preventing switch polingd
    [SwitchThread.cpp]
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2019-04-06 Added provisional electronics housing cover
    Added provisional electronics housing cover. Only slight altering of dimensions necessary once dimensions of LCD, battery pack & buttons are obtained
    [ElectronicsAssembly.SLDASM, ElectronicsHousing.sldprt, ElectronicsHousingCover.sldprt]
2019-04-06 Editing the C script used to display text on the display for it to work with the pins on the PCB board.
2019-04-08 Changes dimensions of connection to servo
    Changed servo gear dimensions to allow more snug fit to servo motor and screw
    [NewServoGear.sldprt, TestNewServoGear5_95mm.SLDPRT, TestNewServoGear6mm.SLDPRT]
2019-04-08 Adding STLs of test gears
    Adding STLs of test gears for the servo motor
    [TestNewServoGear5_95mm.STL, TestNewServoGear6mm.STL]
2019-04-08 Added bolt-guard for outlet pipe
    [BoltGuard.sldprt, BoltGuardAssembly.sldasm]
2019-04-09 Added BoldGuard STL
    [BoltGuard.STL]
2019-04-09 Adjustments for Audio/HDMI/LCD
    Adjustments for Audio jack, HDMI port and LCD screen on the electronics housing
    [ElectronicsAssembly.SLDASM, ElectronicsHousing.sldprt, ElectronicsHousingCover.sldprt]
2019-04-09 Switch holder added
    [switchHolder.SLDPRT, switchHolder.STL]
2019-04-09 Created sorter stand
    [Assembly.SLDASM, BaseDrillGuide.sldprt, SorterStand.STL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]
2019-04-09 dditional test sizes for servo gear
    [TestNewServoGear5_65mm.SLDPRT, TestNewServoGear5_65mm.STL, TestNewServoGear5_75mm.SLDPRT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]
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2019-04-10 Increased bolt-top diameter on Stand
    [SorterStand.STL, SorterStand.sldprt]
2019-04-10 Updated Threaded_Classes to use CMake from separate directory. Made Servo object separate from Threads.
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2019-04-10 Removing no-longer-needed files/folders: Testing_Camera, Classification. Moved PCD and 3D model files into 'hardware'.
    [Assembly.SLDASM, BaseDrillGuide.sldprt, BoltGuard.STL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]
2019-04-11 Updated Electronics casing to fit RPi and new LED PCB
    [ElectronicsAssembly.SLDASM, ElectronicsHousing.STL, ElectronicsHousing.sldprt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]
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2019-04-12 Updated CMakeLists for linking wiringPi libraries. Edited main script and includes for successful compile.
2019-04-12 Reverting to allow branching at this point to a more experimental branch.
    Revert "Adding buffer-usage functionality to classification routine"
    This reverts commit 60cce25d2b257a27df5b04b0ea969c78c1aa961d.
    [Classifier.cpp]
2019-04-13 Image files for wiki and updated switch casing
    [switchHolder.SLDPRT, switchHolder.STL]
2019-04-13 Electronics Cover Completed
    [ElectronicsAssembly.SLDASM, ElectronicsHousing.sldprt, ElectronicsHousingCover.STL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]
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2019-04-14 Integrated Menu into main function, added Menu thread. Still to be tested.
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2019-04-14 Edited Camera to contain Mat conversion of image data. Edited Classifier to reflect this.
2019-04-14 Corrected camera test to reflect recent changes to source files
    [MenuTest.cpp]
2019-04-14 Added beginnings of menu test. Separate class for buttons would make it much easier to test.
2019-04-14 Removed errors from files
    [Display.h, libServo.cpp]
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2019-04-15 Final update to hardware - PCBs & Datasheets
    [glassify.kicad_pcb, glassify.sch, glassify_withPlanes.kicad_pcb]
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
